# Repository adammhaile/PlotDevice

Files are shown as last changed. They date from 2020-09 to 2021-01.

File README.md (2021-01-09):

# PlotDevice
Super compact and simple CoreXY Plotter

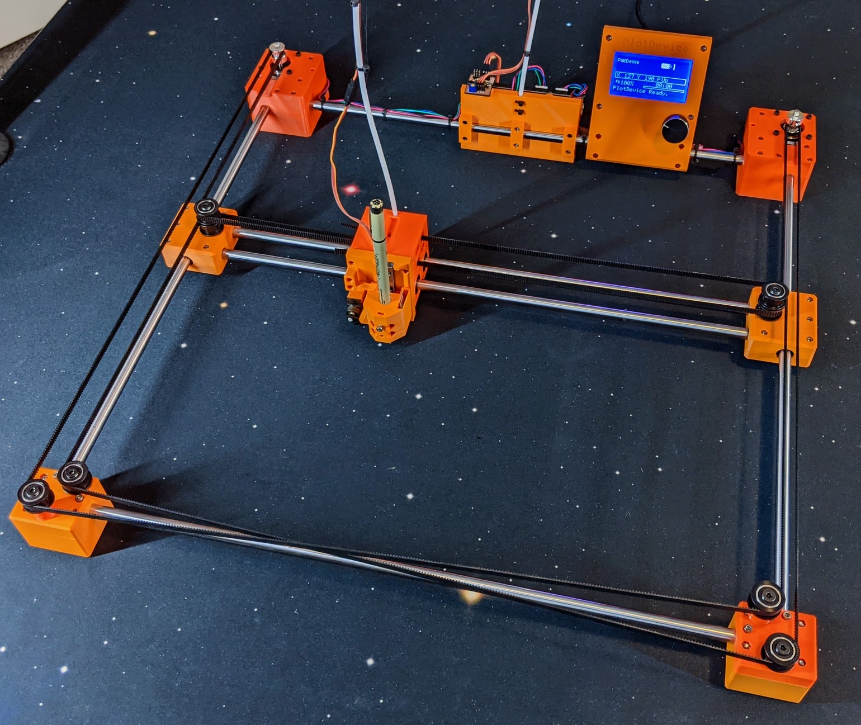
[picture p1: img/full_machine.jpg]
PlotDevice


The PlotDevice is designed to be as simple and cheap as possible without sacrificing quality and speed. While it can be setup with any controller that supports the CoreXY configuration, I have designed it with Marlin and TMC drivers in mind. This allows it to use sensorless homing and therefore making wiring a breeze. The motors are all stationary and you only need to run 3 wires for the servo to the tool head.

The core design calls for 500mm linear rods which results in a roughly 410mm x 350mm working area (depending on tool used). However, you could easily use any length rod to increase or shrink the overall machine size.

The total cost for the specified configuration should be around $300.

## 3D Printed Components

All the necessary CAD models can be found in the [CAD](/CAD) folder and are already oriented correctly for printing. This includes the full [Fusion 360 Design](/CAD/PlotDevice.f3z)

For the items listed as `xN_PartName.stl` note that you must print `N` copies of that item. 

### Print Settings

**PLEASE NOTE:** All components have been designed specifically with the given print settings in mind. There are features of the models that depend on these settings and may not print correctly if not followed.

All components should be printed in PLA with the following settings:

- 0.4mm nozzle diameter
- 0.2mm layer height
- 3 shells / 3 top & bottom lasers
- 25% Grid Infill
- Top & Bottom layers Rectilinear Infill
- NO SUPPORT. None of the components will require any support.

Any other settings would depend on your particular filament and printer capability but I recommend using high quality filament with consistent diameter. I are partial to Printed Solid, Atomic or Prusa brands.

Final word on quality and accuracy: The PlotDevice is designed with relatively tight tolerances so your prints need to be as accurate as possible. If you are unsure, I recommend printing this [calibration cube](https://www.thingiverse.com/thing:1586206) with the filament you want to use first as a test, with the above settings. If any dimension deviates from 20mm by more than 0.1mm, you should spend some time dialing in your extrusion settings for that filament until it is within 0.1mm tolerance.

## Bill of Materials

See the table below for the required components. Please note the following notes:

- The 10mm rods can be basically any length in order to achieve the desired working area. With 500 mm rods the working area will be roughly 410mm on X and 350mm on Y. Simply add or subtract from the 500mm length to change the working area by that size. Note however that the rods **must** be in matched sets.
    - The Y axis is only 2 rods.
    - The X axis requires 4 rods of the same length. 2 for the actual X axis gantry and 2 for the front and back of the frame.
- Limit switches are optional if you use a controller that supports sensorless homing.
- The specified controller will work with the provided Marlin firmware (see link in next section) but for another controller you will need to sort out the configuration yourself.
- 12V or 24V doesn't really matter, but 24V will generally be more responsive.
- Yes, I've specified a Hiwin linear rail for the pen lift. This is very much solving a problem with money and the one place I deviated from the basic ethos of the machine. With shipping expect it to cost $25-30 but I promise it's worth it. Note: ZYLTech will also custom cut MGN9 rails but they will be slightly more expensive than shipping it from RobotDigg in China.
- All nut and bolt counts are approximate and depend on what options you choose. It is highly recommend to purchase more than specified below by at least 15%.

|  Item | Qty | Vendor | Notes |
| --- | --- | --- | --- |
|  M3x25 | 40 | [Albany County Fasters](https://www.albanycountyfasteners.com/Socket-Head-Cap-Screw-3MM-A2-Stainless-Steel-p/5040000.htm) |  |
|  M3x10 | 34 | [Albany County Fasters](https://www.albanycountyfasteners.com/Socket-Head-Cap-Screw-3MM-A2-Stainless-Steel-p/5040000.htm) |  |
|  M3x5 | 8 | [Albany County Fasters](https://www.albanycountyfasteners.com/Socket-Head-Cap-Screw-3MM-A2-Stainless-Steel-p/5040000.htm) |  |
|  M3 Nut | 82 | [Albany County Fasters](https://www.albanycountyfasteners.com/Socket-Head-Cap-Screw-3MM-A2-Stainless-Steel-p/5040000.htm) |  |
|  M2x10 | 2 | [Albany County Fasters](https://www.albanycountyfasteners.com/Socket-Head-Cap-Screw-2MM-A2-Stainless-Steel-p/5020000.htm) | 6 if using physical endstops |
|  M5x55 (low profile) | 6 | [Open Builds](https://openbuildspartstore.com/low-profile-screws-m5-10-pack/) | Be sure to choose the 55mm option |
|  Idler Pulley Kit | 8 | [Open Builds](https://openbuildspartstore.com/smooth-idler-pulley-kit/) | Technically only need the pulley body, 2x 625 bearings, lock nut, and washer from this kit. Could be purchased separately |
|  GT2 Timing Belt | 10 | [ZYLTech](http://www.zyltech.com/fiber-glass-reinforced-2gt-gt2-timing-belt-custom-length-price-per-meter/) | Two ~3m lengths needed. But best to have extra - but a full continuous 10m |
|  GT2 20T Pulley | 2 | [ZYLTech](http://www.zyltech.com/2gt-gt2-6mm-wide-20t-pulley-5mm-6-35mm-or-8mm-bore/) | MUST GET 5mm BORE VERSION!!! |
|  LM10UU Bearing | 4 | [ZYLTech](http://www.zyltech.com/lm10luu-linear-bearing-10mm-long/) | This is the long (55mm) version! |
|  10mm x 500mm Shaft | 6 | [ZYLTech](http://www.zyltech.com/10mm-chrome-plated-hardened-rod-shaft-pre-cut-lengths-300mm-1000mm/) | Be sure to select the 500mm option. |
|  Micro Limit Switch | 2 | [ZYLTech](http://www.zyltech.com/micro-switch-with-1-meter-wire-2a-125vac/) | **Optional if using sensorless homing |
|  MGN9 75mm Rail | 1 | [RobotDigg](https://www.robotdigg.com/product/671/HIWIN-Origin-Miniature-Guideway-Narrow-Linear-Rail) | Be sure to select the **MGN9-1C-75** option |
|  9g Micro Servo | 1 | Various |  |
|  Nema 17 Stepper | 2 | [OMC](https://www.omc-stepperonline.com/index.php?route=product/isearch&search=17HS13-1334S) | Anything Bipolar around 30oz-in and shorter than 45mm should work. With 22+ mm 5mm bore shaft |
|  SKR Mini E3 v2.0 | 1 | [Various](https://www.amazon.com/gp/product/B0882QGFZR/) | v2.0 makes sensorless homing easier |
|  SKR Mini LCD | 1 | [Various](https://www.amazon.com/gp/product/B07NZ9SD26/) | **Optional |
|  12 or 24V @5A+ PSU | 1 | [Various](https://www.amazon.com/gp/product/B07PWZQ4MB/) |  |
|  SeroLaser | 1 | [Maniacal Labs](https://github.com/ManiacalLabs/ServoLaser) | Contact me if you want one |

## Controller

As noted above, any controller and firmware that supports CoreXY should work but sensorless homing would greatly simplify the design so I decided to try it out. Granted, Marlin is generally not a great option for non-3D printer applications but with a few tweaks it's possible to make it work well.

I've created a branch of the latest (as of v2.0.6) Marlin that has been configured for this machine and has the core code slightly modified to handle this application better:

- Added hard coded pen down / up delays to prevent movement starting before the pen is fully down or up.
- Removed Z homing so that a bare `G28` will not fail
- Configured the BLTouch output pins to work with the ServoLaser
- Configured to support M9 to suppress a warning from LightBurn generated gcode which always outputs M9 for Marlin.

You can find this updated code [here](https://github.com/adammhaile/Marlin/tree/PlotDevice) as well as a pre-compiled [firmware.bin in this repo](/firmware.bin).

With this configuration you can control the pen via the marlin "Laser" commands `M3` and `M5`. It's also configured so that anything other than a laser value of 0 will fully deploy the pen, so that:

```
M3 S255 ; pen down
M3 S10  ; also pen down
M3 S0   ; pen up
M5      ; pen up
```

Please note that this also all depends on using the [ServoLaser](https://github.com/ManiacalLabs/ServoLaser). This simple device merely reads the "laser" control signal (configured to output on the BLTouch deploy signal (`PA1`) pin) and converts that to a servo control signal. It provides automatic signal filtering so that you avoid fluttering as well as a built in trimpot that allows you to adjust the range and direction of motion.

The ServoLaser was originally intended to be sold by [Maniacal Labs](https://maniacallabs.com) but we decided to shut down the business before that happened. I do, however, have a couple dozen ServoLaser boards if anyone wants one. Just contact me via adammhaile [at] gmail [dot] com, and I can work out sending you one. Also, the device is not complicated and it would be relatively cheap to have the PCBs fabricated and buy the components - assuming you have the ability to flash the firmware on the ATTiny.

There's probably a way to make Marlin directly output servo signals, triggered by and `M` code but the intent of the ServoLaser was to avoid the need for doing something like that.

## Tool Holders

In the [Fusion 360 Design](/CAD/PlotDevice.f3z), under the `PenLift` component you will find several different pen holder options:

- `GenericPenHolder` - Designed to hold any pen up to 16mm in diameter.
- `PigmaMicronHolder` - Designed for genuine Pigma Micron felt tip "pens". They are amazing and highly recommend since you get get as small as 0.15mm tip diameter. This holder will hold them with a high degree of repeatability (for swapping colors). Knock-off Micron pens will likely not fit.
- `Stabilo88Holder` - Should work with the Stabilo 88 or similar.
- `FountainPen` - Mutli-part to hold a fountain pen (or similar) at an angle. Ensure your pen placement and angle will not cause it to crash into the frame!

All of these holders can be installed with two M3x5 screws (there are 4 holes but 2 on opposite corners works fine) into the MGN rail block. Just ensure it sits between the servo arm and the printed "spring" that's mounted to the pen lift face plate. This "spring" is simply to provide a little down pressure on the pen block, ensuring it doesn't bind in the up position. To that effect, each holder also has a open cavity on the right side - this is for two US nickels as extra weight. This both prevents rail binding as well as provides extra writing pressure on the pen.

But the sky is the limit here. You can use any of these as a starting point to design your own pen holder for *your* pen of choice.

## Build Notes

There will be no step-by-step guide provided. It would likely take me longer to assemble that than it did to design the machine in the first place. My recommendation is to download and load the provided Fusion 360 design and use that as a basic guide of what goes where. But please read through the following notes before beginning:

- All of the rods are held in place by compression from the 3D printed blocks they fit into and you need to make sure you get a tight fit. It the top (in terms of print orientation) is not perfectly flat and smooth you should smooth them out by running that face in a figure-eight pattern over some sand paper on a flat surface. Make sure you can place adjoinging printed parts against each other with no noticable gaps between them.
- Start by securing the 2 bearings in the X axis carriage then insert one rod into each of the bearings. Set aside.
- Place a bearing on each of the Y axis rods
- Pre-insert nuts into the `YRail` bottom parts and keep in place with some tape, if need be
- Set each of the `YRail` bottom parts on a flat surface and place the Y bearings in the recess, and then seat the X axis rods into the 2 slots.
- Place the top of the `YRail` components and secure everything with the M25 bolts. Make sure that the X axis rails are fully seated and square.
- At this point you can place the bottom section of the `Front` and `Motor` components on your builds surface and lay down the Y axis rods and front/back frame rods in the recesses. 
- Note that the front of the X carriage is the size where the bolts holding the bearings are recessed and there are mount holes for the pen mechanism.
- **BEFORE** putting the top of the `Front` components on, be sure to insert the four M5 lock nuts (flat side up) in each of the recesses. These should have come with the OpenBuilds Idler Pulley Kit.
- Before tightening the bolts fully on each corner, move the tool head around a bit and make sure everything runs smoothly and that it doesn't bind and any of the axis limits.
- Once the frame is built you can assembly the idler pulleys and secure them in place with the M5x55mm bolts. The pulleys on the `YRail` will also require an M5 lock nut.
- For the pulleys on the front corners, be sure that you get the correct placement with the standoffs in the correct placement. Refer to the design.
- When tightening the pulley bolts be sure not to overtighten. You want them just tight enough so that they can spin freely. This is why you must use lock nuts.
- Be **very** careful to study the belt pattern in the design before running the belts. Note that the black colored side of each belt in the design represents the side with teeth.
- For the 500mm rod design you will need over 2m of belt for each of the two runs. But I suggest having about 2.5m for each and cutting off the excess when done
- The `Tensioner` component is used both for tensioning and holding the other end of the belt. Start by inserting one end of the belt through the carriage block belt slow **without** a hole next to it, pull it through then slide the belt into the tensioner body. Make sure that the tensioner is inserted into the block with the belt slot open side up and the portion that holds the bolt facing inward.
- Run the belt around the pulleys and then pull the other end of the belt back through the block and through the belt slot with a hole on the same level as where the belt started.
- Pull the belt tight to get an idea of how much belt you need, and then pull it back out a little and insert the belt into a tensioner with a nut inserted. The pull the tensioner and belt back into the block and pass an M3x25mm bolt through the hole on the other side until it engages with the nut. You can then turn the bolt to tension the belt.
- Once this is done with both belts you want to make sure they are roughly the same level of tension. This is not easy so take your time. You made need to fully loosen and reseat the tensioner forward or back on the belt then tighten again.
- To ensure that the belts are of the right tension you can generally tell if the X axis is square to the frame and the belts provide a bit of resistance when pushing on them with one finger.
- You may need to tighten one side then the other until the axis is square *and* the belts are tight enough. During the process move around the tool head manually and make sure that everything still freely moves.
- Hooking up the motors can be a little finicky since there's no specific X or Y motor. Make sure that both motors are wired in the same wire order. Once connected if the tool head moves in the wrong direction or on the wrong axis you make need to either swap the motor connectors or rotate them 180 degrees in the same place. What will be right honestly depends entirely on the motors used.
- Depending on the length of the arms provided with your servo you may need to sand down the tip a little to make sure it doesn't bind up against the pen holder.

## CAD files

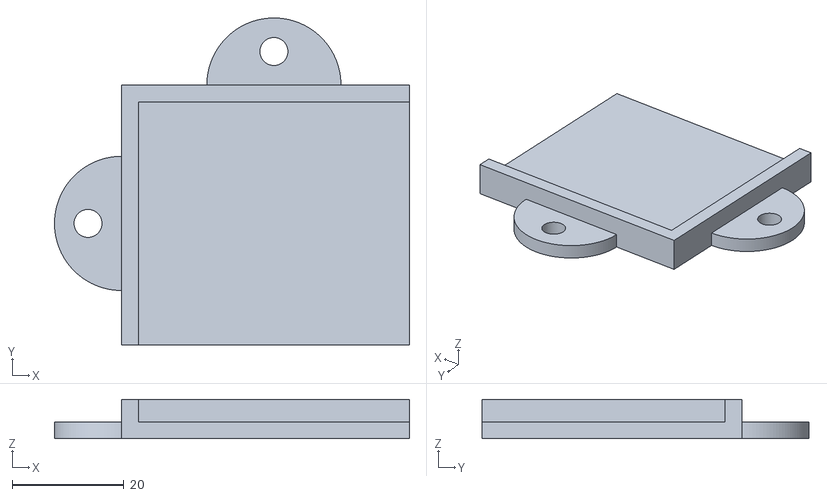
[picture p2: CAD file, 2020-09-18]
CAD/FootFrontRight.stl
63.5 x 58.5 x 7.00

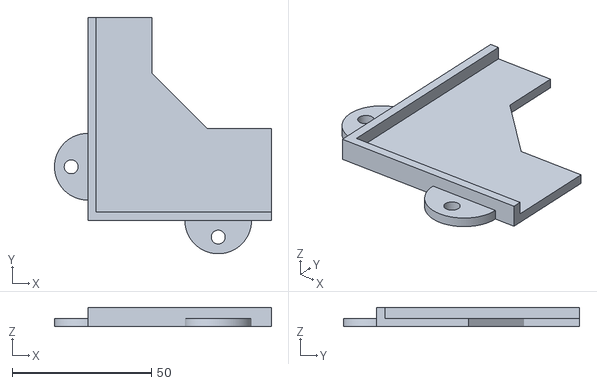
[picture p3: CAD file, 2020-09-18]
CAD/FootBackRight.stl
78.0 x 85.0 x 7.00

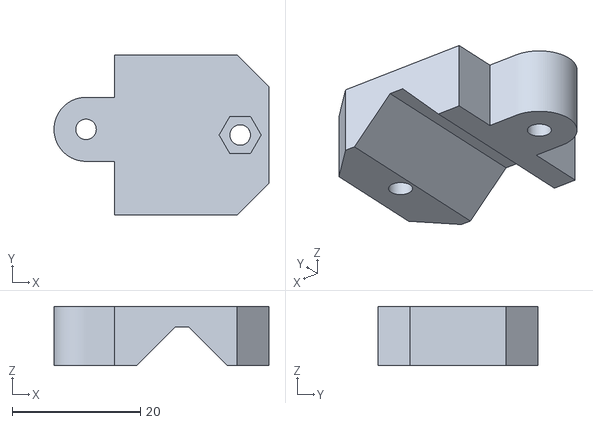
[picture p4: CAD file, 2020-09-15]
CAD/FountainBack.stl
33.6 x 25.0 x 9.25

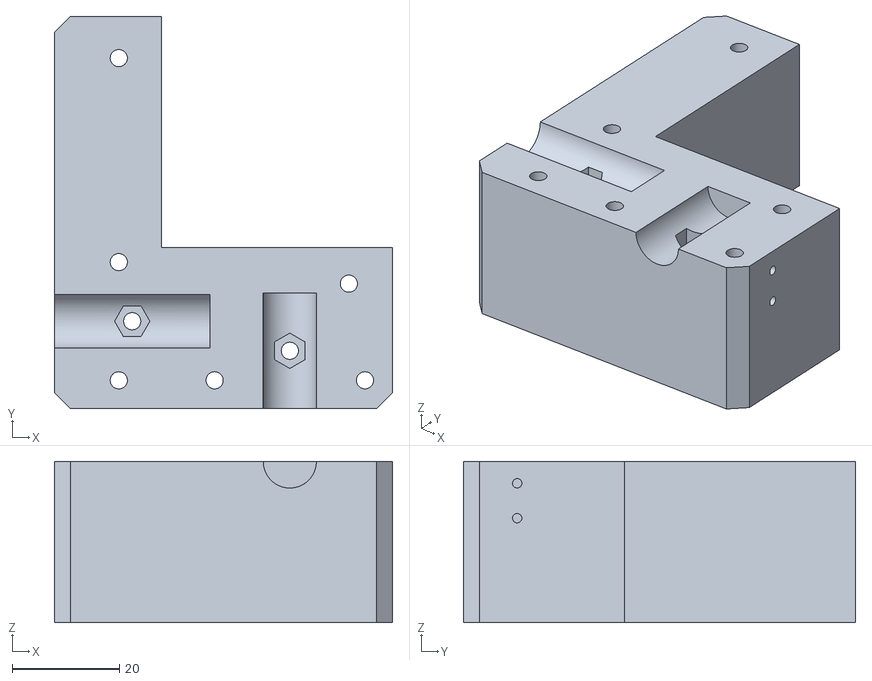
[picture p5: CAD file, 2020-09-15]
CAD/MotorRight_Bottom.stl
63.0 x 73.0 x 30.0

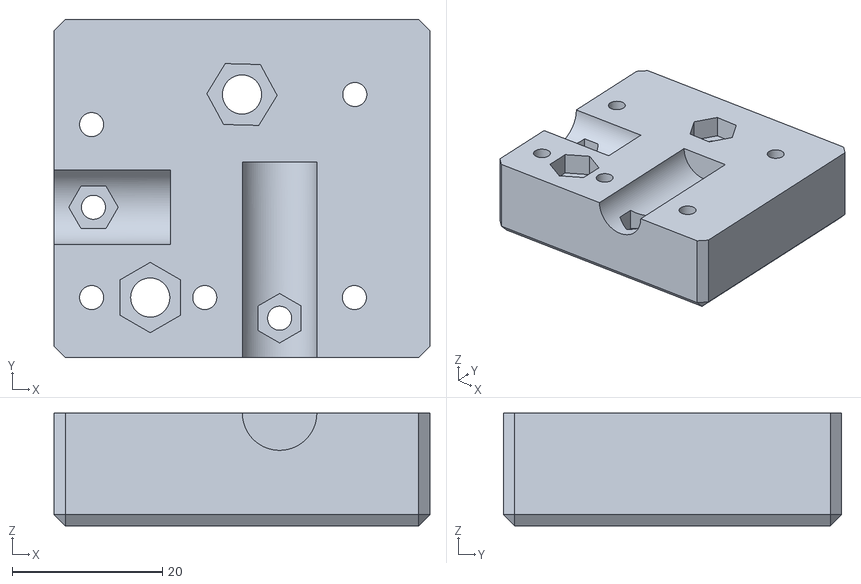
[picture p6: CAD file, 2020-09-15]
CAD/FrontRight_Top.stl
50.0 x 45.0 x 15.0

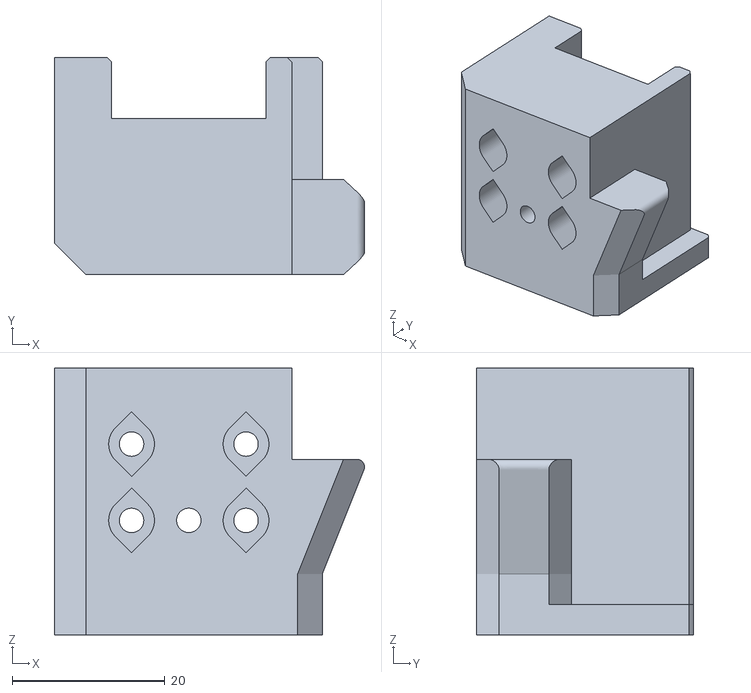
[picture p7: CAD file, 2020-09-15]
CAD/FountainBase.stl
40.6 x 28.5 x 34.9

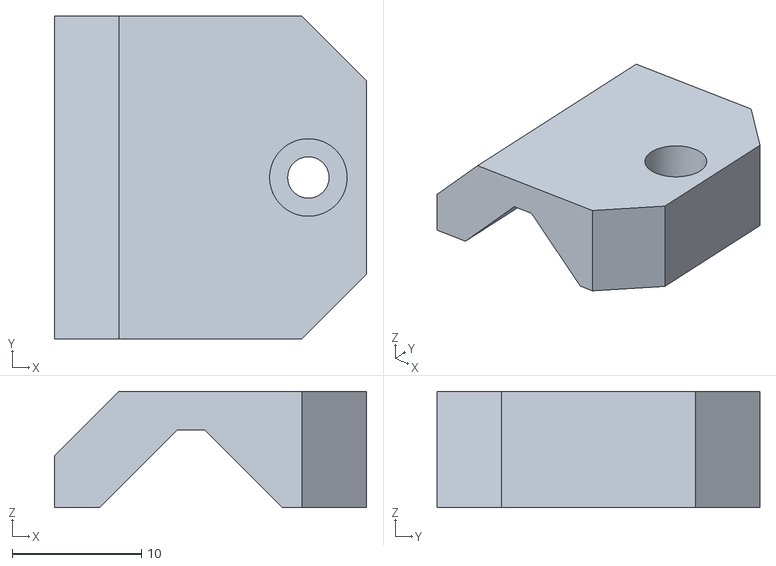
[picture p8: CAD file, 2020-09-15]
CAD/FountainFront.stl
24.2 x 25.0 x 9.00

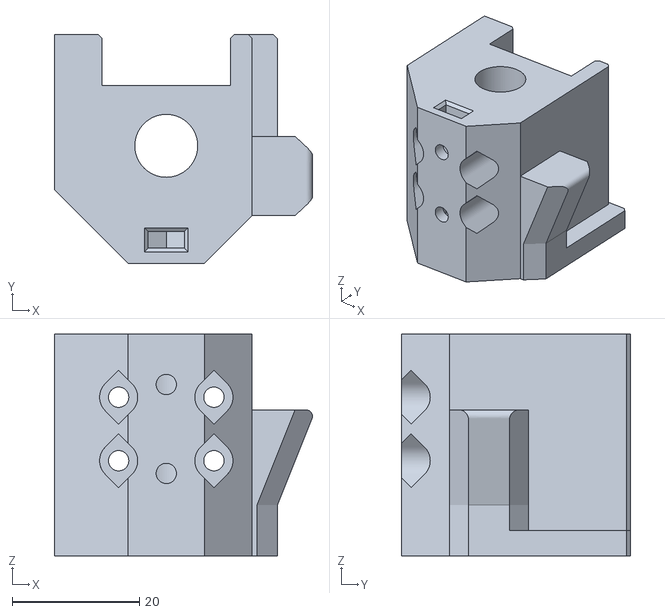
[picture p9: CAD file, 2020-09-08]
CAD/PigmaMicronHolder.stl
40.6 x 36.0 x 35.0

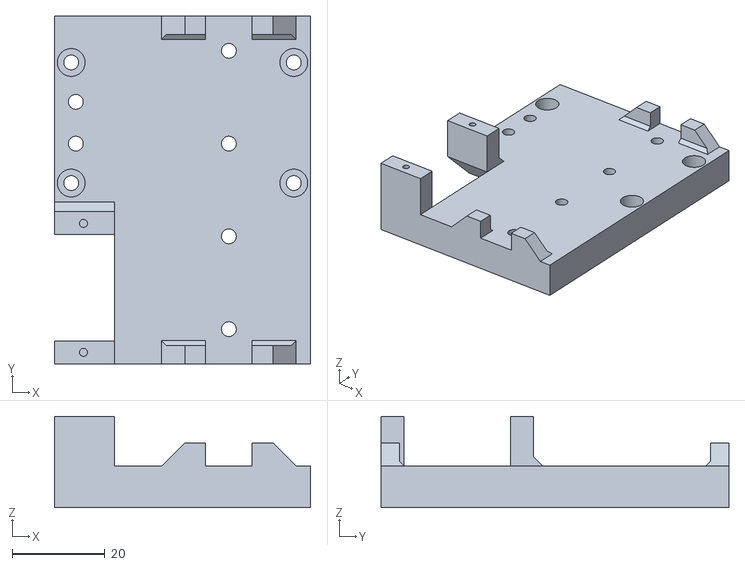
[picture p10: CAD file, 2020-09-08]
CAD/PenLiftBase.stl
55.2 x 75.0 x 19.7

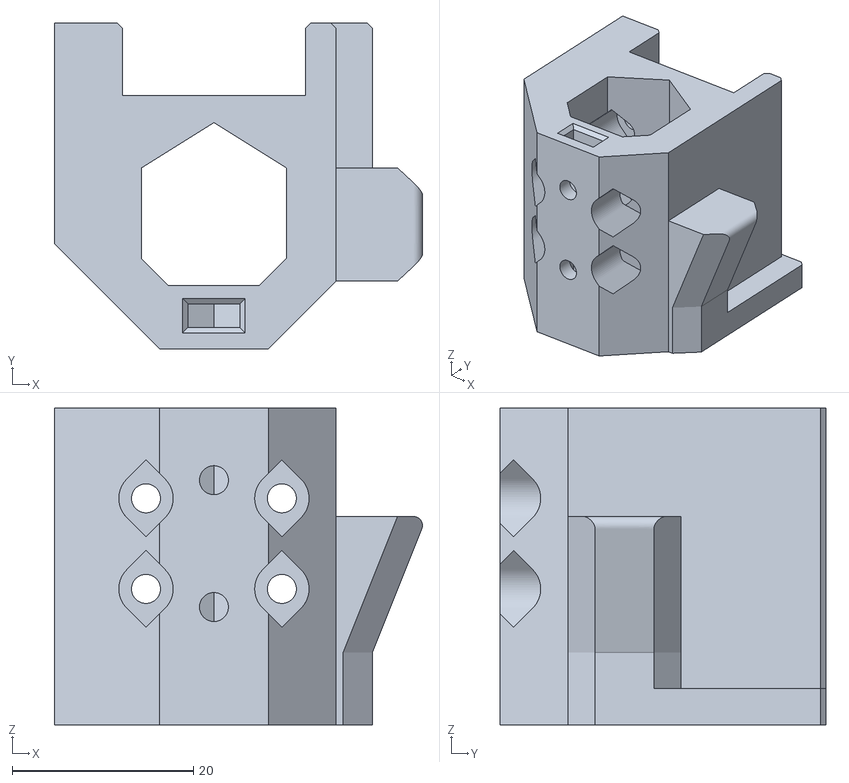
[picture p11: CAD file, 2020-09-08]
CAD/GenericPenHolder.stl
40.6 x 36.0 x 35.0

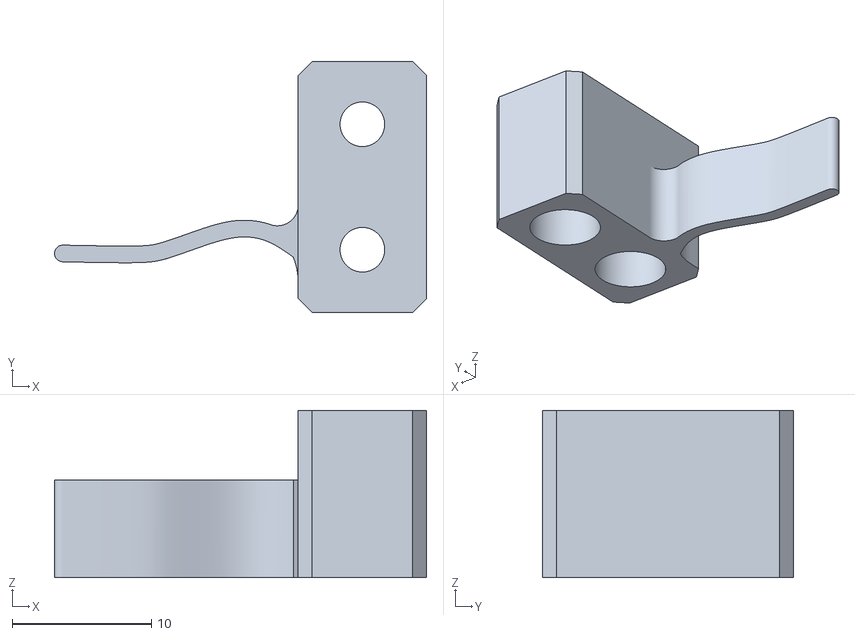
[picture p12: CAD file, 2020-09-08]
CAD/Spring.stl
26.7 x 18.0 x 12.0

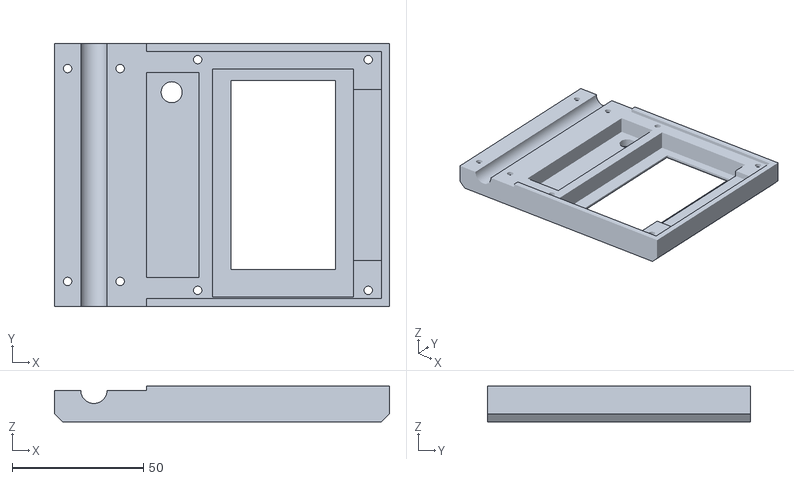
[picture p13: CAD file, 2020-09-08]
CAD/LCDPanelFaceplate.stl
127.5 x 100.0 x 13.6

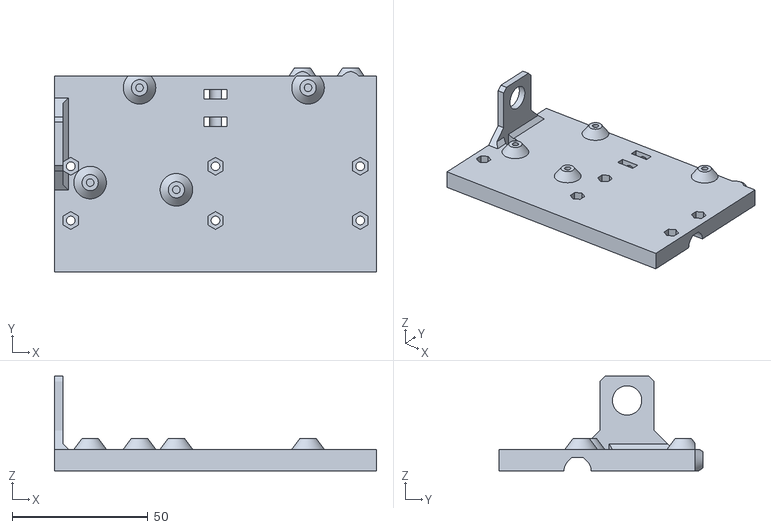
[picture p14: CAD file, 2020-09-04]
CAD/ControllerBase.stl
118.8 x 75.2 x 35.0

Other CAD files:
CAD/FootFrontLeft.stl
CAD/FootBackLeft.stl
CAD/MotorLeft_Bottom.stl
CAD/FrontLeft_Top.stl
CAD/Stabilo88Holder.stl
CAD/FrontLeft_Bottom.stl
CAD/FrontRight_Bottom.stl
CAD/MotorLeft_Top.stl
CAD/MotorRight_Top.stl
CAD/XCarriageBlock.stl
CAD/YRailLeft_Bottom.stl
CAD/YRailLeft_Top.stl
CAD/YRailRight_Bottom.stl
CAD/YRailRight_Top.stl
CAD/x2_FrontPulleyStandoff.stl
CAD/x4_Tensioner.stl
CAD/x5_ControllerClip.stl

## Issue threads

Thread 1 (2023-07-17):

Not an issue, just a thank you!

fbrusch-ik, 2023-07-17:
Hi there,

The pen lift and holder are awesome!
I was looking for inspiration for my own servo z axis and found this but decided to just take it 1:1 because you are even using the correct pen already. Luckily you can buy knockoff MGN9 Rails for less than 10€ straight off amazon now.

Ill probably add a magnetic tool changing system for multicolor prints without intervention.

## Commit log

2020-09-02 Initial design and docs
    [ControllerBase.stl, FromRight_Top.stl, FrontLeft_Bottom.stl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]
2020-09-04 Update design and do rename
    [ControllerBase.stl, LCDPanelFaceplate.stl]
2020-09-08 Update CAD files
    [GenericPenHolder.stl, LCDPanelFaceplate.stl, PenLiftBase.stl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]
2020-09-15 Add fountain holder
    [FountainBack.stl, FountainBase.stl, FountainFront.stl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]
2020-09-18 Add alignment feet
    [FootBackLeft.stl, FootBackRight.stl, FootFrontLeft.stl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]
2020-12-02 Added ServoBudy notes
2021-01-09 Fix BOM links
